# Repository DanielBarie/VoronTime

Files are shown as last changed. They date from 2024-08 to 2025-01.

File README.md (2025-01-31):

# VoronTime
It's Voron Time. 

Built with an LDO kit, rev C.  

Issues along the way:  
- See safety
- The kit differs in some ways from the "official" build. Piecing together the correct instructions isn't the easiest thing to do.
- Chaoticlab CNC mod: Had to re-design/fix some parts.

# (planned) Modifications 
- separate 5V PSU for Raspberry Pi  
- Safety upgrade for heater control  
- Voron Tap, done
- CNC parts for extruder
- CNC parts for XY/Z belt tensioning (done, full CNC kit)
- AngryCam
- Z-Belt Covers with cable guides (done, modified with cutouts for linear rails)

# Things to do after completing mechanics
Following https://docs.ldomotors.com/en/voron/voron2/wiring_guide_rev_c

# SAFETY!
- Disconnect Heater Cables for Hotend and Bed Heating. (Pre-loaded BTT firmware may have these active, so Hotend and/or Bed may get hot).
- Even though having updated the firmware als per [LDO's instructions](https://docs.ldomotors.com/en/voron/voron2/wiring_guide_rev_c)  I had (at least two) cases where the heaters (Hotend, Bed) came on after startup without having activated theses in Klipper. Klipper performed a shutdown because the Hotend was outside its specified temperature range, heating continued anyway?!?) The Hotend (E3D) maxed out at 380°C. This will have to be rectified (probably by adding separate relays into Hotend/Bed Heater circuits which are controlled by Klipper's shutdown state).

First step is setting heater pins to a defined state at Klipper firmware startup (HE0 is hotend, HE1 is bed via SSR):
grafik
grafik (from https://github.com/bigtreetech/BIGTREETECH-OCTOPUS-V1.0/blob/master/Hardware/BIGTREETECH%20Octopus%20-%20SCH.pdf)

Also make sure to have the right config for your Octopus Board. Ours is a v1.1 

## Get the printer into the local wlan
- Maybe do this from the imager (Ctrl-Shift-X), if not:
-  ```sudo raspi-config```
- Set appropriate Country Code
- edit ```/etc/wpa_supplicant/wpa_supplicant.conf```
- see https://wiki.ubuntuusers.de/WLAN/wpa_supplicant/

## Activate ssh
- either in the imager
- or via ```sudo raspi-config```or
- via placing ```ssh``` file in boot partition before inserting sd card into pi

## install useful tools
- ```sudo apt-get install mc```

## Activate unattended upgrades for OS
- ```sudo apt-get install unattended-upgrades```
- Fix stupid Raspberry Pi OS Update Naming: https://raspberrypi.stackexchange.com/questions/38931/how-do-i-set-my-raspberry-pi-to-automatically-update-upgrade
- yes, we might break things by activating this separately from mainsail's os update (but i'd rather be safe than sorry)

## Get the touch screen rotation right:
- see https://docs.ldomotors.com/en/guides/btt_43_rotate_guide
- we choose to edit the config via ssh: ```sudo nano /boot/config.txt```
- when disabling vc4-fkms-v3d we lose external hdmi? or maybe we lose external hdmi because we've rotated the display? (https://www.raspberrypi.com/documentation/accessories/display.html)

## Fix security
We need a password protected web interface
See https://forum.vorondesign.com/threads/protect-your-klipper-printer-mainsail-password-ssl-firewall-rules.469/
- ```apt-get install apache2-utils```
- ```sudo htpasswd -c /etc/nginx/0-passwords.txt <user name>```
- generate ssl/tls certificate: ```openssl req -x509 -nodes -days 36500 -newkey rsa:2048  -keyout /etc/nginx/0-snakeoil.key  -out /etc/nginx/0-snakeoil.crt```
- ```sudo nano /etc/nginx/sites-available/mainsail```
  - comment out ```listen 80 default_server```
  - insert authentication/ssl directives somewhere below [server]:
    ```
    listen 443 ssl default_server;
    ssl_certificate      /etc/nginx/0-snakeoil.crt;
    ssl_certificate_key  /etc/nginx/0-snakeoil.key;
    auth_basic "Velcome to Voron";
    auth_basic_user_file /etc/nginx/0-passwords.txt;
    ```
- ```sudo service nginx restart```

## Update Mainsail:
Just Update all (lower right corner)
grafik

## Install Klipper Installation and Update Helper and KlipperScreen
- Mainsail comes with git installed.
- get kiauh: ```cd ~ && git clone https://github.com/dw-0/kiauh.git```
- run: ```./kiauh/kiauh```
- enter ```1``, you will probably be asked for sudo...
- enter ```5``` to install klipperScreen (takes a while because we need all the packages for a GUI)
- enter ```b```, ```q``` to leave kiauh
- nice, Touchscreen Interface is online.

## Install Klipper Firmware on Octopus BTT Board
- https://docs.vorondesign.com/build/software/octopus_klipper.html
- make is already installed
- ```cd klipper```
- ```make clean```
- ```make menuconfig```
- we have:
  - STM32F446
- all other options as per above guide (only had to change clock to 12MHz)
- DO MAKE SURE TO SET PIN VALUES FOR STARTUP (!PA2,!PA3,!PB10,!PB11)
- compile (```make```), gives firmware bin file
- as for booting the board in DFU mode: That's a huge pain. Sometimes it might work, sometimes it just doesn't for no obvious reason.
- So we go for putting the fimrware on the sd card.
  - don't forget to rename to ```firmware.bin```
  - use a sufficiently small SD card (32GB because of FAT vs exFAT)

## Install Configuration Files for Printer in Mainsail
https://docs.vorondesign.com/build/software/configuration.html
- get it from https://raw.githubusercontent.com/VoronDesign/Voron-2/Voron2.4/firmware/klipper_configurations/Octopus/Voron2_Octopus_Config.cfghttps://raw.githubusercontent.com/Vor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
- rename to ```printer.cfg```
- OR (better): Get the LDO kit version (because we've been using the Rev. C kit): https://github.com/MotorDynamicsLab/LDOVoron2/blob/main/Firmware/octopus-printer-rev-c.cfg  
- upload mainsail -> machine -> config files -> upload:
grafik
- our octopus board's id is ```usb-Klipper_stm32f446xx_52001F000551313133353932-if00``` (```ls /dev/serial/by-id```)
- edit printer.cfg to get basic mechanics going:
  - let mainsail know about the Octopus board:  
   grafik

  - let's have a 350mm printer:    
    grafik
  - another axis with 350mm:  
    grafik
  - Z endstop:  
    grafik

  - z1 stepper enable:  
    grafik

  - Extruder Control pins:
    grafik

  - Nozzle Heater pin:  
    grafik

  - Nozzle heater thermistor:  (change to ATC Semitec)
   grafik

  - Bed Heater:  (change thermistor to ATC Semitec)
    grafik

  - Probe config:
    grafik

  - Gantry corners / probe points config:
    grafik

  -   Next: Check Bed Heating (complains about not heating quickly enough); Extruder Heating works

# Chaoticlab CNC Upgrade:
## XY Joints
Make sure to mount the toothed pulley on the black stand-off.  
grafik    
Regular D2F endstop pod doesn't fit (Y Endstop doesn't reliably trigger). CNC Z Joints are smaller (not as wide) as the printed ones. To fix this, the endstop pod needs to be extended in y-direction (approx. 2mm). Part: modified/extended endstop pod  

## Voron Tap V2
- Belts need to be clipped.  
- Won't activate the X endstop. We need to print https://www.printables.com/de/model/781495-chaoticlab-voron-tap-v2-bracket-for-xy-endstop-pcb/files (TAP_XY_XL.stl) and mount this to the extension bracket intended for the endstop.

### LDO Toolhead PCB ChaoticLab V2 Wiring mismatch  
The LDO toolhead pcb probe connector has a different wiring, doesn't match Chaoticlab's Tap wiring harness: https://www.reddit.com/r/VORONDesign/comments/1aq32nw/chaotic_lab_cnc_tap_not_working/   
Get some JST XH 3 pin connectors, unpinning the one on the wiring harness didn't work for me. Cut it off.   
Original wiring harness connector on the toolhead side:  
toolhead_connector_orig  
New wiring harness connector on the toolhead side:  
toolhead_connector_new  

# Can't connect to MCU?
There's a bug....
https://www.teamfdm.com/forums/topic/1892-beware-latest-klipper-update-breaks-symlink-to-mcu-on-usb-connected-devices/

# Z Belt Covers
Since there is LED strips installed we needed some way of getting the wiring into the electronics compartment. LDO provides STLs for modified Z Belt Covers, see https://github.com/MotorDynamicsLab/LDOVoron2/blob/main/STLs/z_belt_cover_a_led.stl  
These will do the job but there's better ones: https://mods.vorondesign.com/details/LzEFU0RDHXUarF7y69x2Q  
Our Z linear rails are too close, so We modified these with cutouts for the linear rails:
- [Z Belt Cover A, STEP-File](cable_routing_z_belt_cover_a_mod_v2_cutout_rail.4%20v1.step)
- [Z Belt Cover B, STEP-File](cable_routing_z_belt_cover_b_mod_v2_cutout_rail.4%20v1.step)

# Issues still open:
- check groundung of DIN rails
- check grounding of frame
- check 5V Octopus Adapter according to https://news.ldomotors.com/2023/01/19/octopus-power-adapter-issue/
- square gantry (done, heat soaking will need to be done after having installed panels)
- install lcd cover

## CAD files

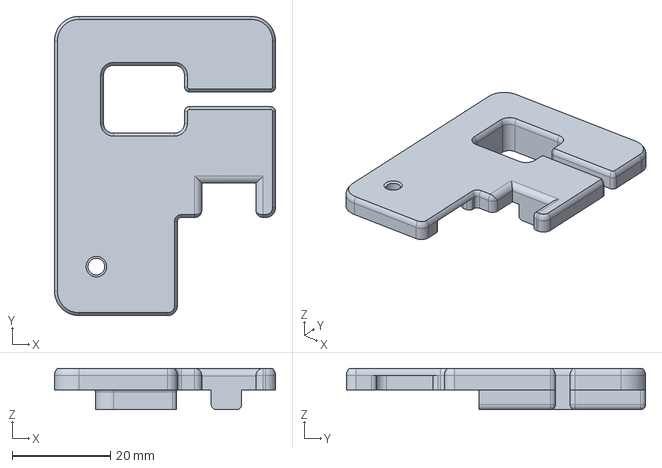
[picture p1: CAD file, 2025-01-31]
cable_routing_z_belt_cover_a_mod_v2_cutout_rail.4 v1.step
45.0 x 61.0 x 8.40 mm

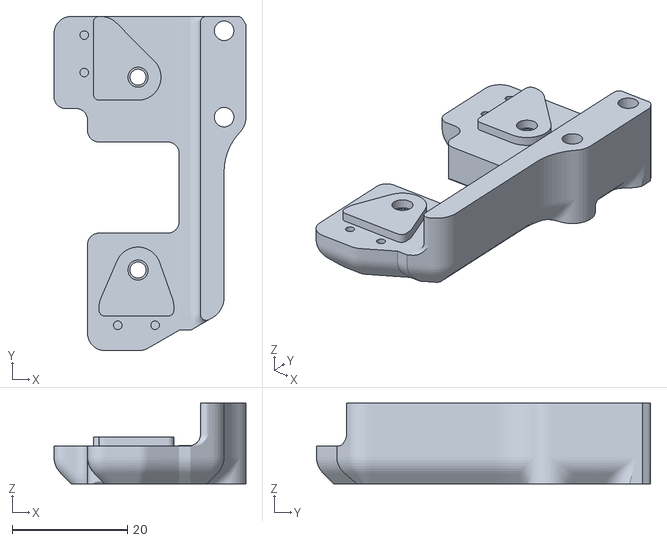
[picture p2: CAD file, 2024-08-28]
endstop_pod_extended_2.0.stl
33.4 x 58.0 x 14.0

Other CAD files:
cable_routing_z_belt_cover_b_mod_v2_cutout_rail.4 v1.step
